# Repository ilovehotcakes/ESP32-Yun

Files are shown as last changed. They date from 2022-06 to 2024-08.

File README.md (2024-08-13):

# ESP32 Yun
An open-source, end-to-end hardward & software solution for motorizing your smart home.

ESP32 Yun is an affordable, reliable, and user-friendly wireless stepper motor controller that works with two-phase bipolar stepper motors. It comes with a web user-interface for intuitive controls and HTTP restful APIs for custom integrations.

Under active development.



<p align="center">
    
</p>

## Features
* 📡 WiFi-based: no need for extra hub
* 🔄 Closed-loop system: motor can be manually moved without losing track of its position
* 🛑 Automatic stalling detection and stopping: preventing injuries and protecting the motor
* 🤖 Custom hardware: few parts, cheap and relatively easy to assemble
* 🖥️ Web UI: no need to download app to control motor or change settings, works on desktop/mobile devices
* 🌐 HTTP restful APIs: easy to create integrations for smart home platforms
* 😶 Extremely quiet, won't even wake a baby!
* 🚀 Can go really fast!

Please see [demo video](images/demo_video.mp4) for full demonstration!

## Building your own
There are three components: electronics, firmware, and mounting hardware. ⚠️Requires basic knowledge of flashing firmware and soldering.

### Requirements:
* [USB-to-TTL serial adatper](https://www.amazon.com/dp/B07WX2DSVB) to upload the firmware
* Soldering iron, wires, and [JST PH connectors](https://www.amazon.com/dp/B0731MZCGF)/[crimper](https://www.amazon.com/dp/B00YGLKBSK)
* Two-phase bipolar stepper motor, such as a [Nema 11](https://www.amazon.com/dp/B00PNEPK94/)
* Magnet for the rotary encoder
* Power supply: 3.3-9V, 1.2A max
* (Optional) 3D printer for the motor mount

### 1. Electronics
Please refer to the [*electronics*](electronics/) folder.

**[[schematic](electronics/schematic.png)][[gerber files](electronics/gerber.zip)][[bom](electronics/bom.csv)][[pick-and-place file](electronics/pick_and_place.csv)]**
<p align="center">
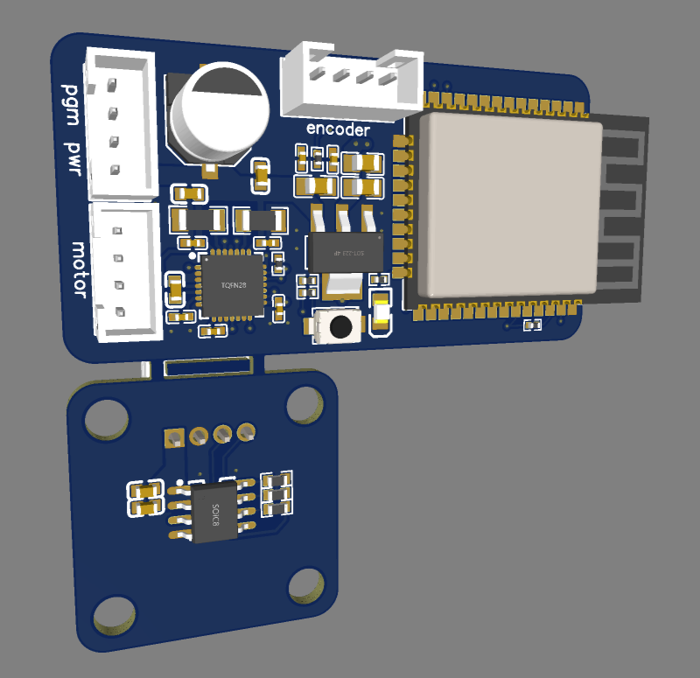
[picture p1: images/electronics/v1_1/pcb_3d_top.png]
    
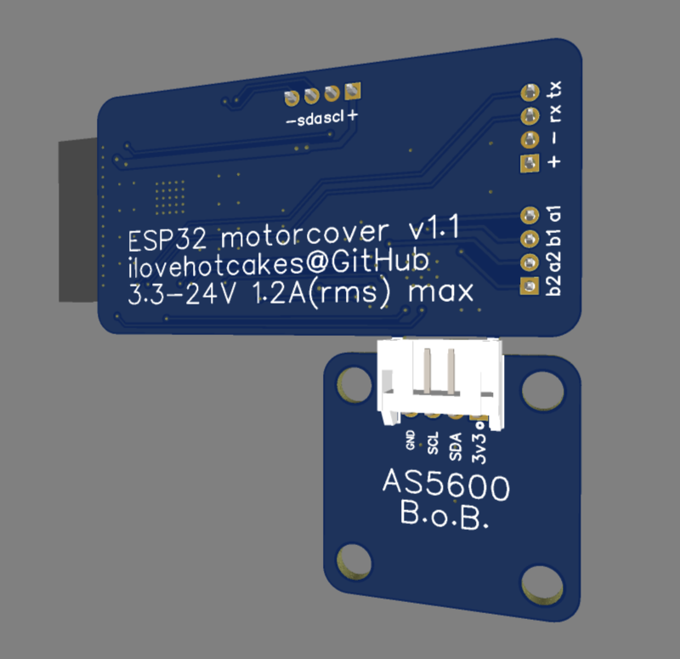
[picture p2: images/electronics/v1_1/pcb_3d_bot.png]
    
</p>

### 2. Firmware
Flash the firmware via [VSCode](https://code.visualstudio.com/) + [PlatformIO](https://platformio.org/install/ide?install=vscode).

#### Dependencies:
* espressif32@3.5.0
* [TMCStepper@^0.7.3](https://github.com/teemuatlut/TMCStepper)
* [FastAccelStepper@^0.27.5](https://github.com/gin66/FastAccelStepper/tree/0.27.5)
* [robtillaart/AS5600@^0.4.1](https://github.com/RobTillaart/AS5600/tree/0.4.1)
* [ESPAsyncWebServer](https://github.com/me-no-dev/ESPAsyncWebServer)
* [ArduinoJson@^7.0.4](https://github.com/bblanchon/ArduinoJson/tree/v7.0.4)
* [LittleFS_esp32@^1.0.6](https://github.com/lorol/LITTLEFS/tree/1.0.6)

#### Steps:
1. Clone this repository.
2. Double check and set proper current sense resistor value in **platformio.ini**.
3. Set the USB-to-TTL serial adatper's logic level to **3V3** and plug it in to the computer.
4. Keep holding the button on ESP32 Yun and start flashing the firmware.
5. Once the IDE begins data transmition, connect the four wires from ESP32 Yun to the adapter: **RX to TXD**, **TX to RXD**, **+ to VCC**, and **− to GND**.
6. Let go of the button once the firmware starts uploading. Unplug ESP32 motorcover after the firmware has finished uploading.

### 3. Mounting hardware
You can find the stl and pre-sliced files under the [*cad*](cad/) folder. To mount the magnet for the rotary encoder, it is recommended to use the manget gluing jig to make sure that the magnet is centered on the axis-of-rotation; otherwise, it could affect the accuracy of the rotary encoder.

#### Parts:
* Nema 11 motor mount: [[**stl**](cad/nema_11_motor_mount.stl)]
* AS5600 magnet gluing jig: [[**stl**](cad/prototype/magnet_gluing_jig_v1.stl)]
* AS5600 rotary encoder mount: [[**stl**](cad/as5600_mount.stl)]

<p align="center">
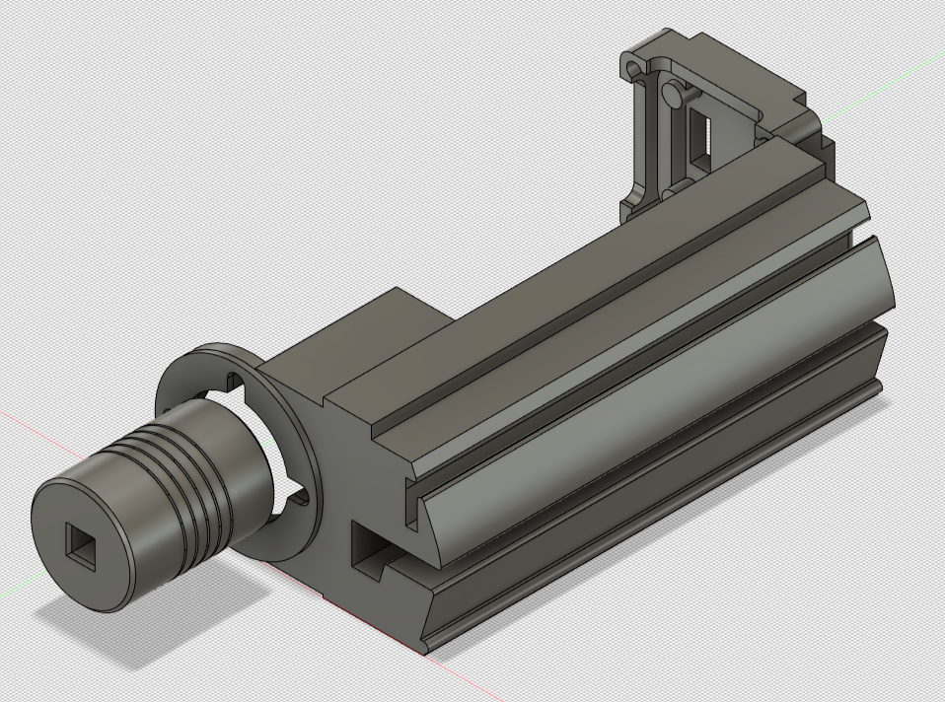
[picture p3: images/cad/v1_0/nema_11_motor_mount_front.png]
    
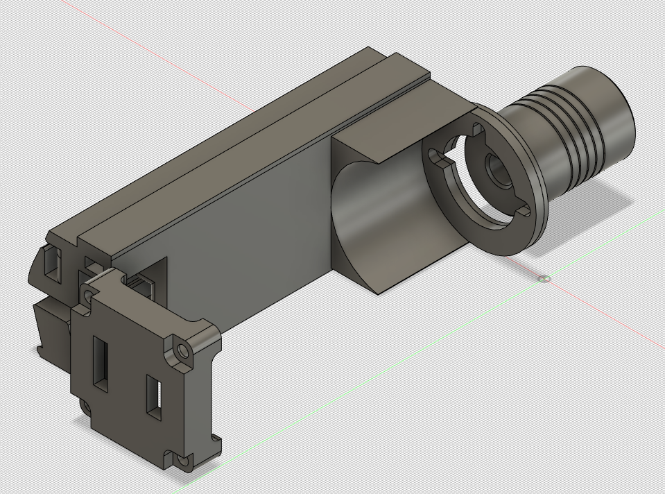
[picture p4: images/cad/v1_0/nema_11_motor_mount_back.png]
    
    </br>
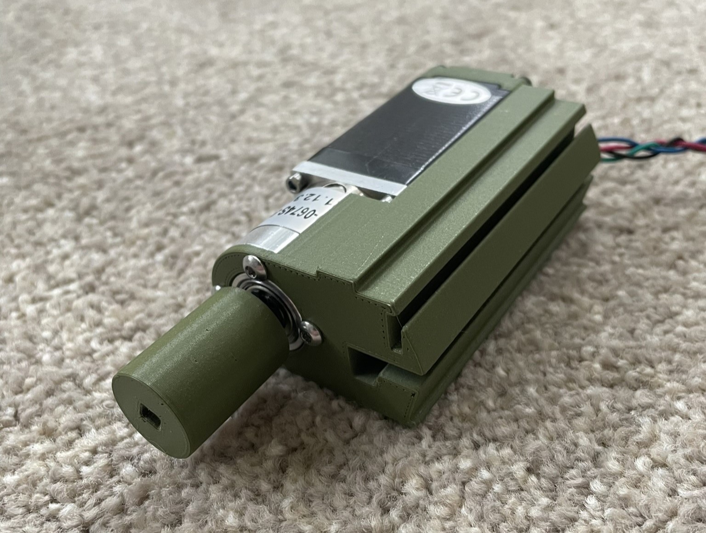
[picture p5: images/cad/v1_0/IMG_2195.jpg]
    
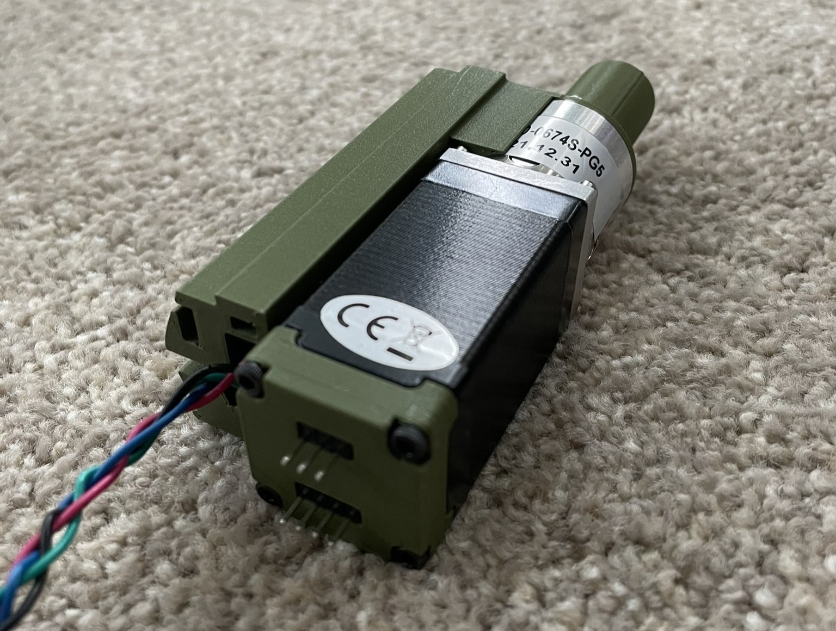
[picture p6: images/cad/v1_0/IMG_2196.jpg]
    
</p>

## Usage
During the first time booting up, ESP32 Yun is put into setup mode and it functions as a WiFi access point. Connect to it with your device like you would connect to a WiFi network. After connection is established, open a web browser and go to the IP address **[192.168.4.1]()** to access the web UI. There you can enter your WiFi network credentials and change other settings.

### HTTP Restful API
All RestAPIs are implemented as HTTP GET requests. To control the motor or change any settings, use [http://&lt;ESP32-YUN-IP-ADDRESS&gt;/&lt;URI&gt;?&lt;PARAM&gt;=&lt;VALUE&gt;](). For example: [http://192.168.4.1/motor?percent=0](). There are four URIs: motor, system, wireless, and json.

#### Motor params:
* stop: stop the motor
* percent: move the motor to the specified percentage
* step: move the motor to the specified step
* forward: run the motor foward continuously
* backward: run the motor backward continuously
* set-min: set the beginning endpoint
* set-max: set the ending endpoint
* zero: set the current motor position to zero
* standby: put the motor driver into standby to reduce power consumption
* sync-settings: sync open/closing settings for current, velocity, and acceleration 
* velocity: set both opening and closing velocity
* opening-velocity: set opening velocity
* closing-velocity: set closing velocity
* acceleration: set opening and closing acceleration
* opening-acceleration: set opening acceleration
* closing-acceleration: set closing acceleration
* current: set opening and closing current
* opening-current: set opening current
* closing-current: set closing current
* direction: change the direction of the motor
* full-steps: set the number of full steps per turn
* microsteps: set the number of subvisions per full step
* stallguard: enable/disable stallguard
* coolstep-threshold: set threshold to enable stallguard and coolstep
* stallguard-threshold: set threshold to trigger stallguard
* fastmode: set to exclusively use fastmode, i.e. SpreadCycle
* fastmode-threshold: set threshold to automatically switch over to fastmode

#### System params:
* sleep: put ESP32 Yun into standby
* restart: restart the system
* reset: reset all settings to factory settings
* name: rename the system

#### Wireless params:
* setup: setup mode
* ssid: ssid of your WiFi network
* password: passowrd of your WiFi network

#### Json:
Use HTTP GET request [http://&lt;ESP32-YUN-IP-ADDRESS&gt;/json]() to get all settings in a Json object.

### Button
* Toggle setup mode: press and hold down for 5 seconds till the led turns on
* Factory reset: press and hold down for 15 seconds till the led turns off after it turns on at 5 seconds

### (Optional) tuning StallGuard4
StallGuard4 (SG) is a feature of the motor driver, TMC2209, which provides automatic stall detection and stopping. SG requires some trial-and-error as well as some patience to get it working correctly. Please refer to the [TMC2209 datasheet](https://www.analog.com/media/en/technical-documentation/data-sheets/TMC2209_datasheet_rev1.09.pdf), chapter 16, page 70.

## In the works
* Custom drivers to reduce dependency and firmware size
* Updating PCB so little-to-no soldering is required
* Replace ESP32 WROOM 32E so USB-to-TTL is not required to flash the firmware
* BLE support
* Ultra-low power for battery application

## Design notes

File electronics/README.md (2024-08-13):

# Electronics
Here are two ways to acquire the electronics: **(1)** directly order printed circuit boards from online PCB services, or **(2)** buying breakout boards and assembling them on a breadboard.

## Option 1 - Ordering PCB from JLCPCB:
1. Download [gerber.zip](gerber.zip) and upload it to [JLCPCB.com](https://jlcpcb.com/). The only setting that needs to be changed is the **"Impedance Control"**. Select **"Yes"** and choose **"JLC0416H-3313"** once the dialog pops up.
2. If you prefer to have the PCB assembled by JLCPCB (additional cost), download the [pick-and-place.csv](pick_and_place.csv) and [bom.csv](bom.csv), and select **"PCB Assembly"**. Click on **"Confirm"** to go the next page.
3. Upload the pick-and-place and bom files. Click **"Process BOM & CPL"** and **"Continue"** when the error pops up. The error is for the missing connectors which will need to be manually solder once the PCBs arrive.
4. Place the order.
5. Once the PCBs arrive, solder connectors **J1-J4** and separate the AS5600 break-off board from the main board.
6. Crimp some 4-pin JST PH connectors and connect the stepper motor to the **"motor"** connector, power supply to the **"pwr"** connector, and AS5600 breakoff board to the **"encoder"** connector.
<p align="center">
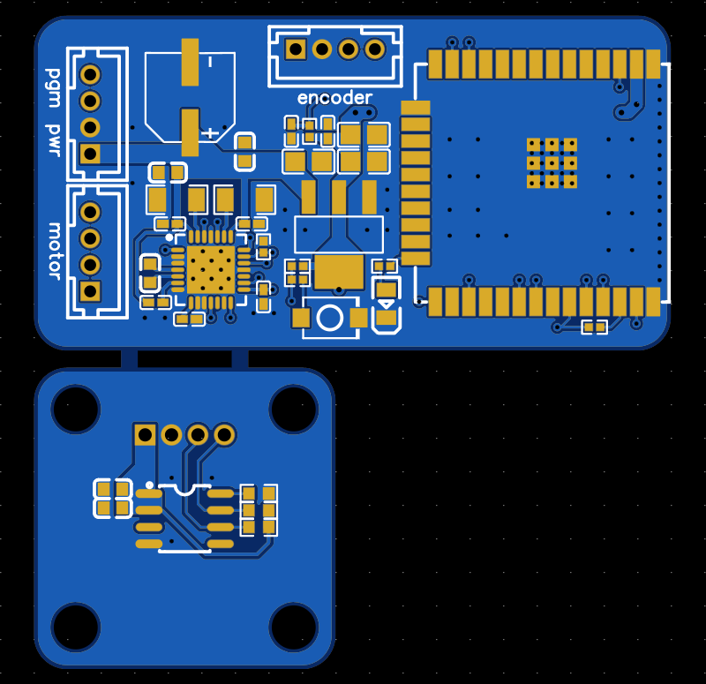
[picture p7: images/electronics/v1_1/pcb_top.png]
    
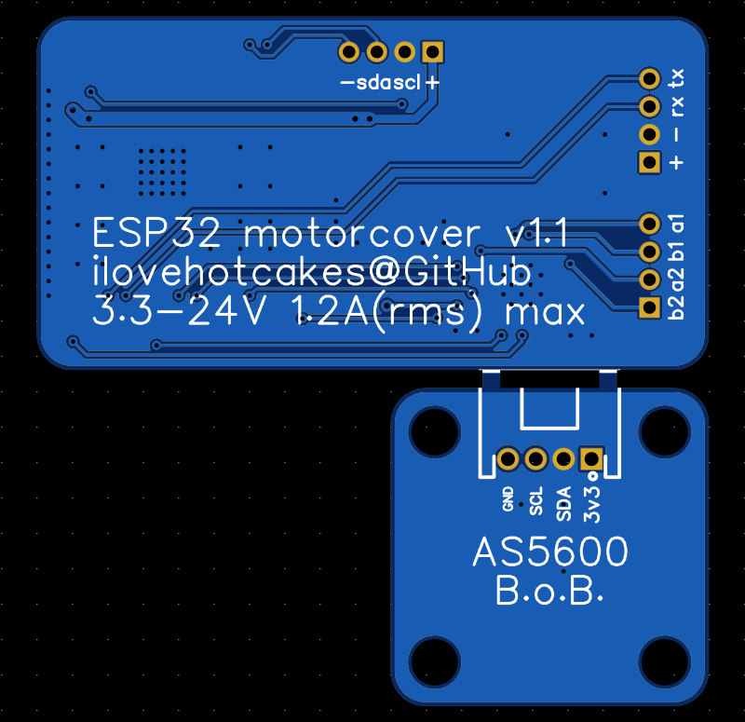
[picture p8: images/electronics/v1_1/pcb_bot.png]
    
</p>

## Option 2 - Breadboarding with breakout modules:
Both [TMC2209](https://www.amazon.com/dp/B07ZQ3C1XW) and [AS5600](https://www.amazon.com/dp/B09KGWC1PT/) come in breakout board packages which can be purchased from Amazon/AliExpress and assembled on a solderless breadboard. Please refer to this version of the [bom](prototype/bom.csv) and reference the schematic to assemble the circuit.
<p align="center">
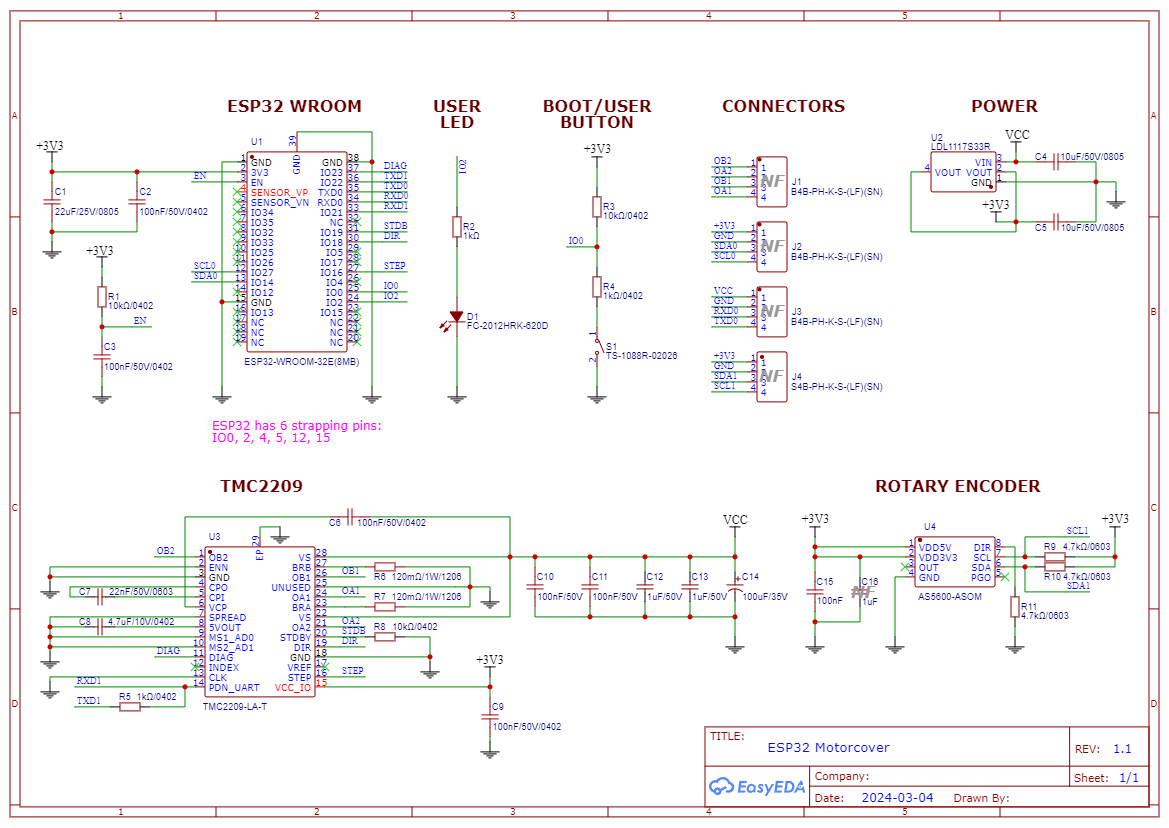
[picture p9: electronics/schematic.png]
    
</p>

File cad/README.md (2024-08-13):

# Mounting Hardware
If you don't own a 3D printer, consider online 3D printing services like [Shapeways](https://www.shapeways.com/) or local print farms.

## Recommendations
Print in TPU to reduce vibration and noise.

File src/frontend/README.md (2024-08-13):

The frontend is consisted of a single index.html webpage, however, it is split into three separate files in this directory: index.html, index.css, index.js for ease of development. The final index webpage needs to be assembled into one html file and stored as a string variable so it can be read by the wireless task.

The python script, index_script.py, reads and assembles the files from this directory and writes the output file index.h to the include directory. If you are using platformio, the frontend will be automatically generated when building the project; else, manually run the python script or copy-and-paste the files together.

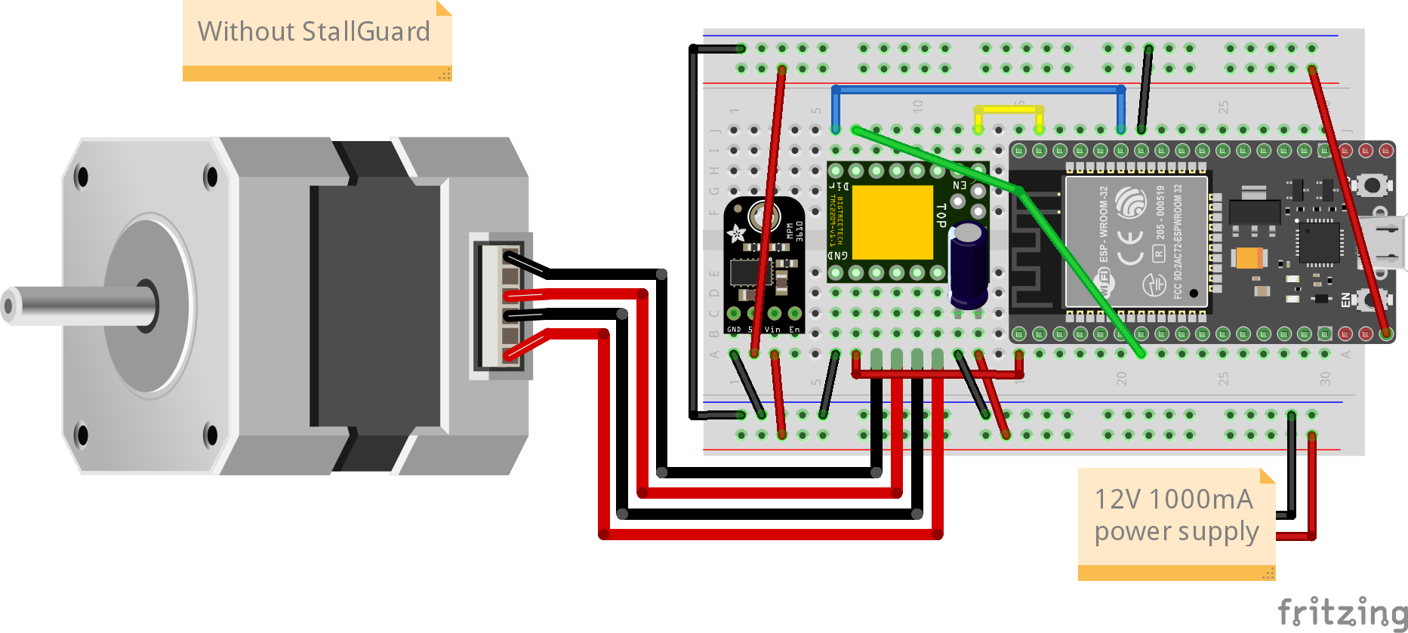
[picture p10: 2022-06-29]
electronics/prototype/esp32_motorcover.png

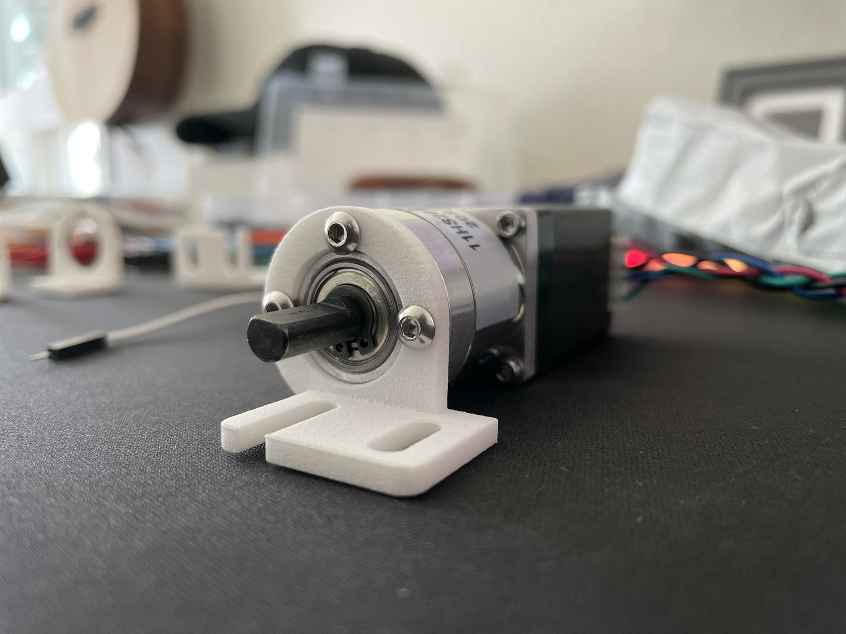
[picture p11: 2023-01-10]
images/cad/prototype/motor_in_mount.jpg

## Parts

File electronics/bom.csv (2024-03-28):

ID | Name | Designator | Footprint | Quantity | Manufacturer Part | Manufacturer | Supplier | Supplier Part | Price
1 | 100nF | C15 | C0603 | 1 | CC0603KRX7R9BB104 | YAGEO(国巨) | LCSC | C14663 | 0.002
2 | 100uF/35V | C14 | CAP-SMD_BD6.3-L6.6-W6.6-FD | 1 | EEEFT1V101AP | PANASONIC(松下) | LCSC | C128464 | 0.236
3 | ESP32-WROOM-32E(8MB) | U1 | WIFI-SMD_ESP32-WROOM-32E | 1 | ESP32-WROOM-32E-N8 | ESPRESSIF(乐鑫) | LCSC | C701342 | 3.284
4 | LDL1117S33R | U2 | SOT-223-4_L6.5-W3.5-P2.30-LS7.0-BR | 1 | LDL1117S33R | ST(意法半导体) | LCSC | C435835 | 0.177
5 | TMC2209-LA-T | U3 | QFN-28_L5.0-W5.0-P0.50-BL-EP | 1 | TMC2209-LA-T | TRINAMIC | LCSC | C2150710 | 2.449
6 | AS5600-ASOM | U4 | SOIC-8_L5.0-W4.0-P1.27-LS6.0-BL | 1 | AS5600-ASOM | ams(艾迈斯半导体) | LCSC | C79815 | 1.441
7 | 22uF/25V/0805 | C1 | C0805 | 1 | CL21A226MAQNNNE | SAMSUNG(三星) | LCSC | C45783 | 0.025
8 | 100nF/50V/0402 | C2,C3,C6,C9 | C0402 | 4 | CL05B104KB54PNC | SAMSUNG(三星) | LCSC | C307331 | 0.005
9 | 10uF/50V/0805 | C4,C5 | C0805 | 2 | GRM21BR61H106KE43L | muRata(村田) | LCSC | C440198 | 0.07
10 | 22nF/50V/0603 | C7 | C0603 | 1 | CL10B223KB8NNNC | SAMSUNG(三星) | LCSC | C21122 | 0.004
11 | 4.7uF/10V/0402 | C8 | C0402 | 1 | CL05A475MP5NRNC | SAMSUNG(三星) | LCSC | C23733 | 0.006
12 | 100nF/50V | C10,C11 | C0402 | 2 | CL05B104KB54PNC | SAMSUNG(三星) | LCSC | C307331 | 0.005
13 | 1uF/50V | C12,C13 | C0603 | 2 | CL10A105KB8NNNC | SAMSUNG(三星) | LCSC | C15849 | 0.005
14 | 10kΩ/0402 | R1,R3,R8 | R0402 | 3 | 0402WGF1002TCE | UNI-ROYAL(厚声) | LCSC | C25744 | 0.001
15 | 1kΩ | R2 | R0402 | 1 | 0402WGF1001TCE | UNI-ROYAL(厚声) | LCSC | C11702 | 0.001
16 | 1kΩ/0402 | R4,R5 | R0402 | 2 | 0402WGF1001TCE | UNI-ROYAL(厚声) | LCSC | C11702 | 0.001
17 | 120mΩ/1W/1206 | R6,R7 | R1206 | 2 | STE1206M1W0R120F | WALTER(华德) | LCSC | C201309 | 0.054
18 | 4.7kΩ/0603 | R9,R10,R11 | R0603 | 3 | 0603WAF4701T5E | UNI-ROYAL(厚声) | LCSC | C23162 | 0.001
19 | TS-1088R-02026 | S1 | SW-SMD_L3.9-W3.0-P4.45 | 1 | TS-1088R-02026 | XUNPU(讯普) | LCSC | C455280 | 0.049
20 | FC-2012HRK-620D | D1 | LED0805-R-RD | 1 | NCD0805R1 | 国星光电 | LCSC | C84256 | 0.012

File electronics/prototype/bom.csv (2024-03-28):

Item | Cost (incl. tax) | Quantity | Shipping | Subtotal | Vendor | Links
NEMA bipolar stepper motor | 33.34 | 5 | 33.12 | 199.82 | Stepperonline | https://www.omc-stepperonline.com/nema-11-stepper-motor-bipolar-l-45mm-w-gear-ratio-5-1-planetary-gearbox-11hs18-0674s-pg5
ESP32 node mcu | 12.1 | 5 |  | 60.5 | Amazon | https://www.amazon.com/dp/B0718T232Z
Buck convertor | 5.95 | 5 | 7.99 | 37.74 | Mouser | https://www.mouser.com/ProductDetail/485-4739
TMC2209 UART stepper driver | 34.12 | 1 |  | 34.12 | Amazon | https://www.amazon.com/gp/product/B07YW7BM68
Coupling | 14.96 | 1 |  | 14.96 | Amazon | https://www.amazon.com/gp/product/B07MPFJGZW
100uF capacitor | 6.82 | 1 |  | 6.82 | Amazon | https://www.amazon.com/gp/product/B07Y3F194W
Solderless breadboard | 6.59 | 1 |  | 6.59 | Amazon | https://www.amazon.com/gp/product/B07LF71ZTS
Power supply | 17.51 | 2 |  | 35.02 | Amazon | https://www.amazon.com/gp/product/B07N18XN84
Wires | 14.86 | 1 |  | 14.86 | Amazon | https://www.amazon.com/gp/product/B07Z4W6V6R
Mounting bracket (Shapeways) | 6.04 | 5 | 9.99 | 40.2 | Shapeways | resources/mounting_bracket_v3.stl
Screws | 10 | 1 |  | 10
AS5600 | 16.99 |  |  | 16.99 | Amazon | https://www.amazon.com/dp/B097QNG1CN
Total |  |  |  | 477.62

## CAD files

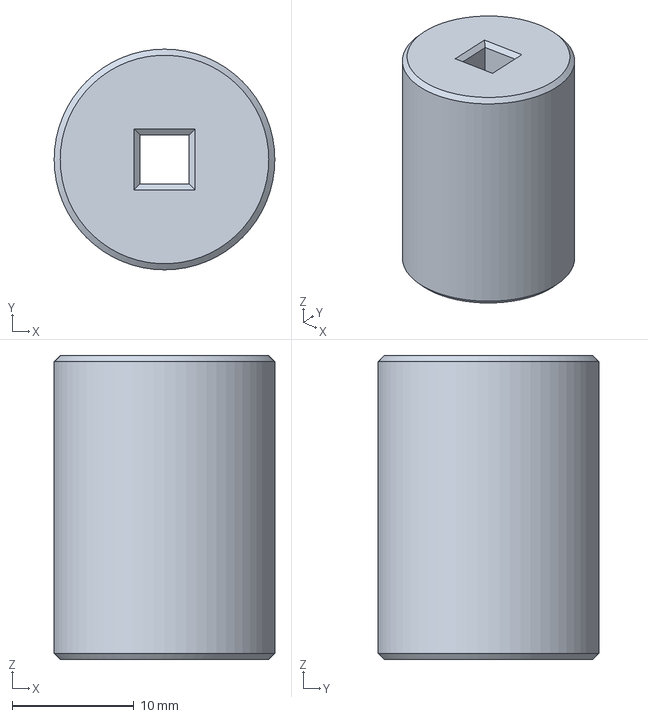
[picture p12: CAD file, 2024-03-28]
cad/coupling.3mf
18.1 x 18.1 x 25.0 mm

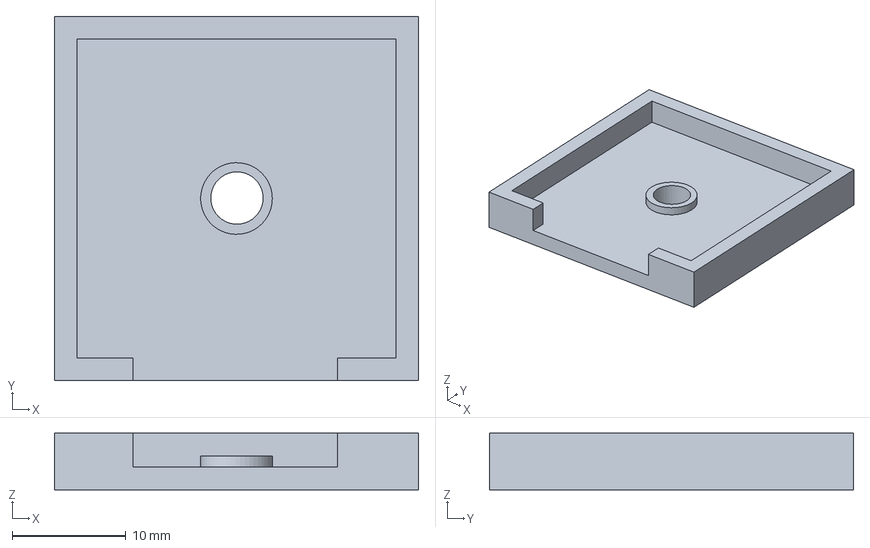
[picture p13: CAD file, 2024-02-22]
cad/prototype/magnet_gluing_jig_v1.3mf
32.0 x 32.0 x 5.00 mm

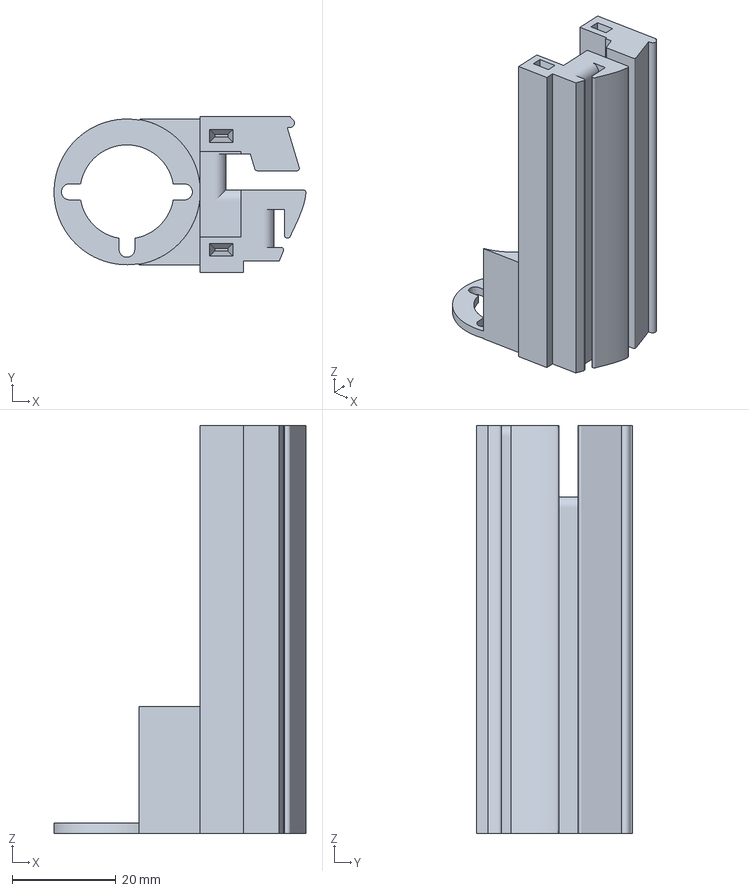
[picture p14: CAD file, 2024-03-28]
cad/nema_11_motor_mount.3mf
48.7 x 30.2 x 78.8 mm

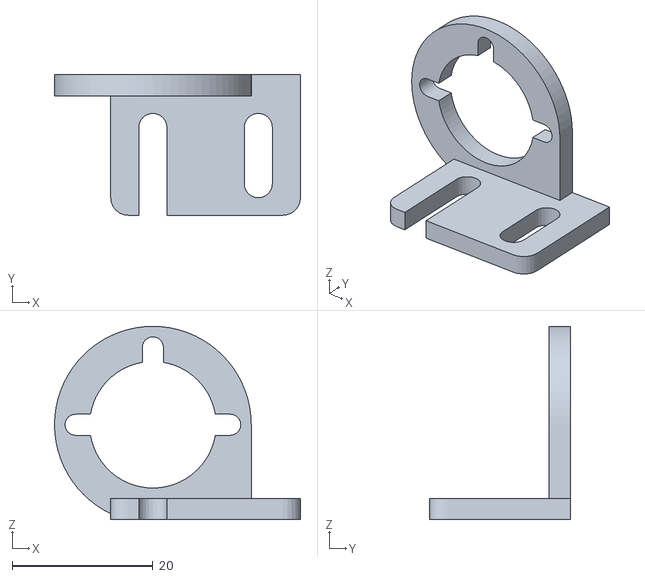
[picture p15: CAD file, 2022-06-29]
cad/prototype/nema11_mount_v3.stl
35.0 x 20.0 x 27.5

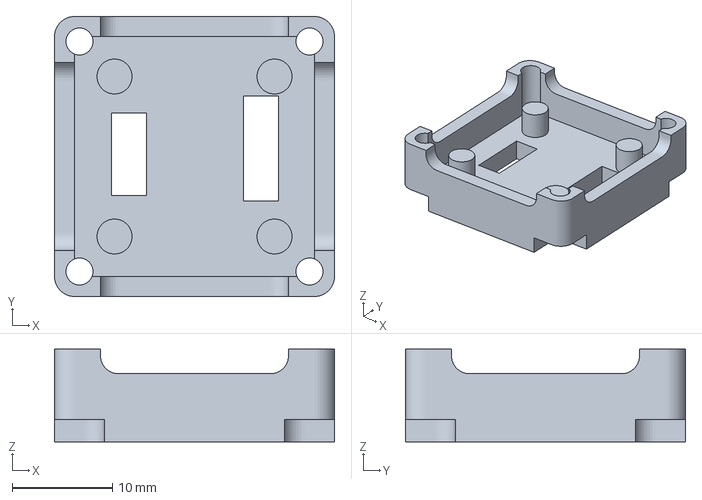
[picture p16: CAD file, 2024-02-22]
cad/as5600_mount.3mf
28.0 x 28.0 x 9.25 mm

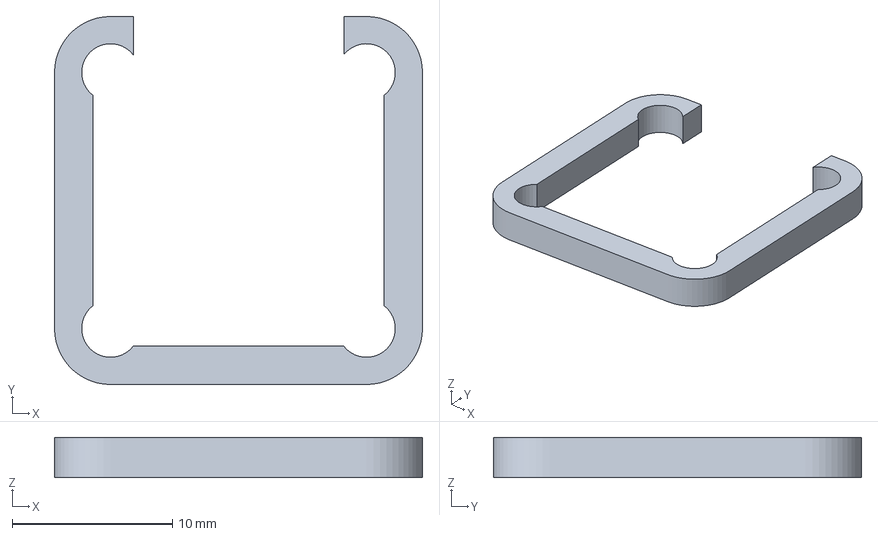
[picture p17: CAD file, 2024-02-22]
cad/as5600_mount_insert.3mf
23.0 x 23.0 x 2.50 mm

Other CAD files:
cad/prototype/nema11_mount_v3_mirrored.stl
cad/as5600_mount.stl
cad/as5600_mount_insert.stl
cad/coupling.stl
cad/magnet_gluing_jig_v1.stl
cad/nema_11_motor_mount.stl
cad/prototype/magnet_gluing_jig_v1.stl

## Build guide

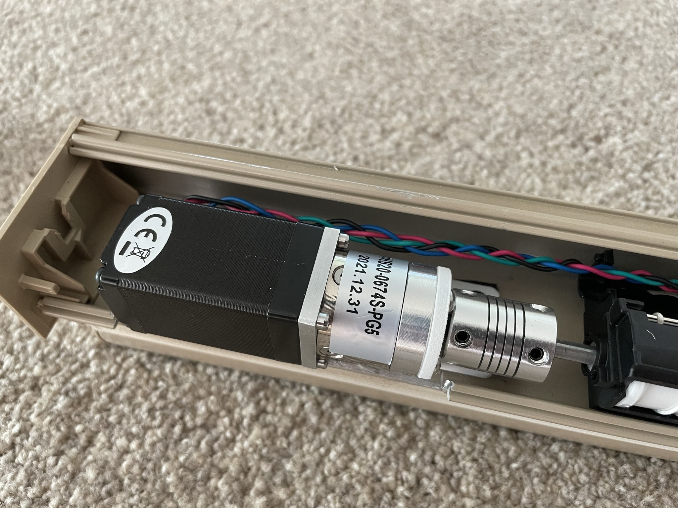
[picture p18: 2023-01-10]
images/cad/prototype/motor_installed.jpg

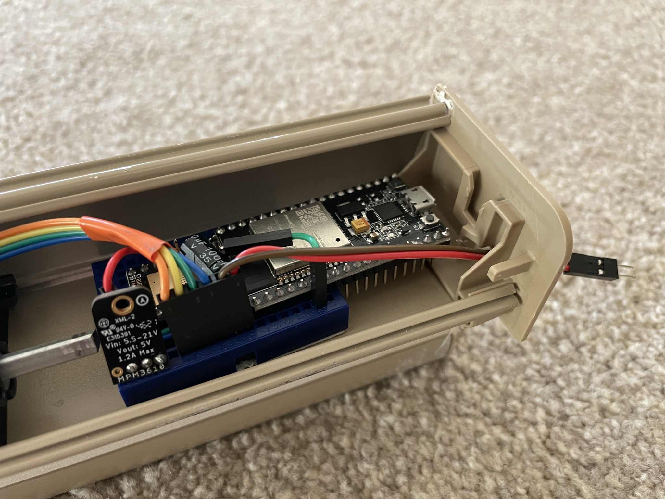
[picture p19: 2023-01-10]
images/electronics/prototype/controller_installed.jpg

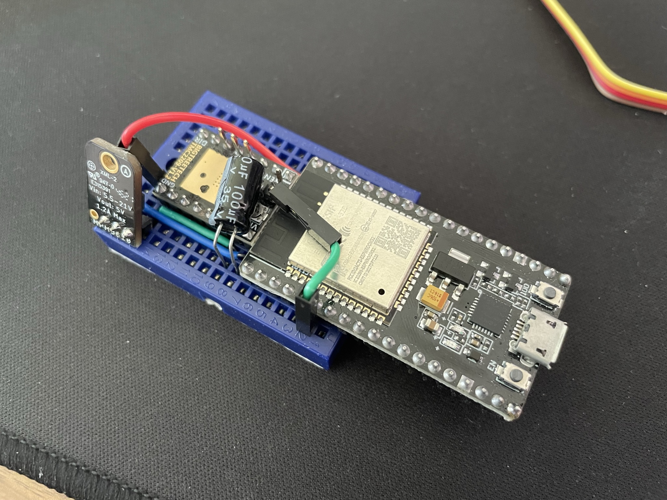
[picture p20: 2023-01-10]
images/electronics/prototype/assembled_controller.jpg

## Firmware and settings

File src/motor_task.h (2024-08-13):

#pragma once
/**
    motor_task.h - A class that contains all functions to control a two-phase bipolar stepper motor.
    Author: Jason Chen, 2022

    The MCU sends PWM signals to the stepper motor driver, TMC2209, to control the current to the
    motor and thereby moving the motor. Higher voltages and current generate more torque and higher
    RPMs. To operate the driver: (1) start the driver by taking it out of STANDBY, and (2) ENABLE
    the motor coils. Both are done automatically.

    The position of the system is absolute and it is translated between 3 different methods:
        (1) "Position" refers to the encoder's position, used for internal position tracking
        (2) "Steps" refers to the motor's position, used for moving the motor
        (3) "Percentage" refers to the overall percentage, used by UI
**/
#include <HardwareSerial.h>       // Hardwareserial for uart
#include <FunctionalInterrupt.h>  // std:bind()
#include <TMCStepper.h>
#include <FastAccelStepper.h>
#include <AS5600.h>
#include "task.h"


#define DEFAULT_MOTOR_FULLSTEPS   200      // NEMA motors have 200 full steps/rev
#define DEFAULT_ENCODER_POSITIONS 4096.0f  // AS5600 absolute position is 12-bit


class MotorTask : public Task {
public:
    MotorTask(const uint8_t task_core);
    ~MotorTask();
    void addWirelessTask(Task *task);
    void addSystemSleepTimer(xTimerHandle timer);

protected:
    void run();

private:
    // TMCStepper library for interfacing with the stepper motor driver hardware, to read/write
    // registers for setting speed, acceleration, current, etc.
    TMC2209Stepper driver_ = TMC2209Stepper(&Serial1, R_SENSE, DRIVER_ADDR);

    // User adjustable TMC2209 motor driver settings, updated to driver registers via UART
    bool  driver_stdby_  = false;
    bool  sync_settings_ = false;  // If false, opeining/closing settings are different values
    float open_velocity_ = 3.0;
    float clos_velocity_ = 3.0;
    float open_accel_    = 0.5;
    float clos_accel_    = 0.5;
    int   open_current_  = 200;
    int   clos_current_  = 75;
    bool  direction_     = false;
    int   microsteps_    = 2;
    int   full_steps_    = DEFAULT_MOTOR_FULLSTEPS;
    bool  stallguard_en_ = true;
    int   coolstep_thrs_ = 0;
    int   stallguard_th_ = 10;
    bool  spreadcycl_en_ = false;
    int   spreadcycl_th_ = 33;

    // FastAccelStepper library for generating PWM signal to the stepper driver to move/accelerate
    // and stop/deccelerate the stepper motor.
    FastAccelStepperEngine engine_ = FastAccelStepperEngine();
    FastAccelStepper *motor_       = NULL;

    // None user adjustable motor states. Managed by MotorTask.
    int8_t  last_updated_percent_ = -100;
    volatile bool stalled_        = false;
    portMUX_TYPE stalled_mux_     = portMUX_INITIALIZER_UNLOCKED;
    // bool motor_opening = false;
    // bool motor_closing = false;
    // bool motor_move_completed = false;

    // Rotary encoder for keeping track of motor's actual position because motor could slip and
    // cause the position to be incorrect. A closed-loop system.
    AS5600 encoder_;

    // Keeping track of the overall position via encoder's position and then  convert it into
    // motor's position and percentage.
    int32_t encod_offset_      = 0;
    int32_t encod_pos_         = 0;
    int32_t encod_max_pos_     = static_cast<int32_t>(DEFAULT_ENCODER_POSITIONS) * 10;
    int   total_steps_         = full_steps_ * microsteps_;
    float motor_encoder_ratio_ = total_steps_ / DEFAULT_ENCODER_POSITIONS;
    float encoder_motor_ratio_ = DEFAULT_ENCODER_POSITIONS / total_steps_;

    Task *wireless_task_;              // To receive messages from wireless task
    xTimerHandle system_sleep_timer_;  // To prevent system from sleeping before motor stops

    void stallguardInterrupt();
    void loadSettings();  // Load motor settings from flash
    bool prepareToMove(bool check, bool direction);
    void move(bool direction);
    void moveToStep(int target_step);
    void moveToPercent(int target_percent);
    void stop();
    bool setMin();
    bool setMax();
    bool zeroEncoder();
    bool motorEnable(uint8_t enable_pin, uint8_t value);
    void calculateTotalSteps();
    inline int getPercent();
    inline int positionToStep(int encoder_position);
    // For quick configuration guide, please refer to p70-72 of TMC2209's datasheet rev1.09
    // TMC2209's UART interface automatically becomes enabled when correct UART data is sent. It
    // automatically adapts to uC's baud rate. Block until UART is finished initializing so ESP32
    // can send settings to the driver via UART.
    void updateMotorSettings(float velocity, float acceleration, int current);
    void driverStartup();
    void driverStandby();
};

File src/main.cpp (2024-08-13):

/**
    Aurthor: Jason Chen, 2022
    Licence: TODO

    An ESP32-based low-powered wireless motor controller that works with two-phase bipolar stepper
    motors. It is a closed-loop system so it is capable of keeping track of its position even when
    the motor is off.

    You can use it to motorize and automate the opening & closing of blinds/shades/windows etc.
**/
#include "system_task.h"
#include "motor_task.h"
#include "wireless_task.h"


static WirelessTask wireless_task(0);  // Running on core0
static SystemTask system_task(0);      // Running on core0
static MotorTask motor_task(1);        // Running on core1


void setup() {
    // Initializing serial output if compiled
    LOG_INIT(115200, LogLevel::INFO);

    if (!LITTLEFS.begin(true)) {
        LOGE("Failed to mount filesystem");
    }

    // setCpuFrequencyMhz(80);

    system_task.init();
    system_task.addMotorTask(&motor_task);
    system_task.addWirelessTask(&wireless_task);

    wireless_task.init();
    wireless_task.addMotorTask(&motor_task);
    wireless_task.addSystemTask(&system_task);
    wireless_task.addSystemSleepTimer(system_task.getSystemSleepTimer());

    motor_task.init();
    motor_task.addWirelessTask(&wireless_task);
    motor_task.addSystemSleepTimer(system_task.getSystemSleepTimer());

    // Delete setup/loop task
    vTaskDelete(NULL);
}


void loop() {}

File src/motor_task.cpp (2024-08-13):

#include "motor_task.h"


MotorTask::MotorTask(const uint8_t task_core) : Task{"MotorTask", 8192, 1, task_core} {}
MotorTask::~MotorTask() {}


void MotorTask::run() {
    pinMode(DIR_PIN, OUTPUT);
    pinMode(STEP_PIN, OUTPUT);
    pinMode(STBY_PIN, OUTPUT);
    pinMode(DIAG_PIN, INPUT);

    // Using UART(Serial1) to read/write data to/from TMC2209 stepper motor driver
    Serial1.begin(115200, SERIAL_8N1, RXD1, TXD1);
    while(!Serial1);

    // FastAccelStepper setup
    engine_.init(1);
    motor_ = engine_.stepperConnectToPin(STEP_PIN);
    assert(motor_ != NULL);
    motor_->setEnablePin(100, false);
    motor_->setExternalEnableCall(std::bind(&MotorTask::motorEnable, this,
                                  std::placeholders::_1, std::placeholders::_2));
    motor_->setDirectionPin(DIR_PIN);
    motor_->setAutoEnable(true);     // Automatically enable/disable motor output when moving
    motor_->setDelayToDisable(200);  // 200ms off delay

    driverStandby();

    // AS5600 rotary encoder setup
    encoder_.begin(SDA_PIN, SCL_PIN);
    // assert(encoder_.isConnected());
    Wire.setClock(1000000);         // Increase I2C bus speed to 1MHz which is AS5600's max bus speed
    encoder_.setConfigure(0x2904);  // Hysteresis=1LSB, fast filter=10LSBs, slow filter=8x, WD=ON
    LOGI("Encoder automatic gain control(56-68 is preferable): %d/128", encoder_.readAGC());

    loadSettings();
    // int start = 0;
    while (1) {
        // start = micros();
        encod_pos_ = encoder_.getCumulativePosition() - encod_offset_;
        motor_->setCurrentPosition(positionToStep(encod_pos_));

        if (xQueueReceive(queue_, (void*) &inbox_, 0) == pdTRUE) {
            LOGI("MotorTask received message: %s", inbox_.toString().c_str());
            switch (inbox_.command) {
                case MOTOR_STOP:
                    stop();
                    break;
                case MOTOR_PERECENT:
                    moveToPercent(inbox_.parameter);
                    break;
                case MOTOR_STEP:
                    moveToStep(inbox_.parameter);
                    break;
                case MOTOR_FORWARD:
                    move(false);
                    break;
                case MOTOR_BACKWARD:
                    move(true);
                    break;
                case MOTOR_SET_MIN:
                    setMin();
                    break;
                case MOTOR_SET_MAX:
                    setMax();
                    break;
                case MOTOR_ZERO:
                    zeroEncoder();
                    break;
                case MOTOR_STANDBY:
                    if (inbox_.parameter == 1) driverStandby();
                    else driverStartup();
                    break;
                case MOTOR_SYNC_STTNG:
                    setAndSave(sync_settings_, static_cast<bool>(inbox_.parameter), "sync_settings_");
                    break;
                case MOTOR_VLCTY:
                    setAndSave(open_velocity_, inbox_.parameterf, "open_velocity_");
                    setAndSave(clos_velocity_, inbox_.parameterf, "clos_velocity_");
                    break;
                case MOTOR_OP_VLCTY:
                    setAndSave(open_velocity_, inbox_.parameterf, "open_velocity_");
                    break;
                case MOTOR_CL_VLCTY:
                    setAndSave(clos_velocity_, inbox_.parameterf, "clos_velocity_");
                    break;
                case MOTOR_ACCEL:
                    setAndSave(open_accel_, inbox_.parameterf, "open_accel_");
                    setAndSave(clos_accel_, inbox_.parameterf, "clos_accel_");
                    break;
                case MOTOR_OP_ACCEL:
                    setAndSave(open_accel_, inbox_.parameterf, "open_accel_");
                    break;
                case MOTOR_CL_ACCEL:
                    setAndSave(clos_accel_, inbox_.parameterf, "clos_accel_");
                    break;
                case MOTOR_CURRENT:
                    setAndSave(open_current_, inbox_.parameter, "open_current_");
                    setAndSave(clos_current_, inbox_.parameter, "clos_current_");
                    break;
                case MOTOR_OP_CURRENT:
                    setAndSave(open_current_, inbox_.parameter, "open_current_");
                    break;
                case MOTOR_CL_CURRENT:
                    setAndSave(clos_current_, inbox_.parameter, "clos_current_");
                    break;
                case MOTOR_DIRECTION:
                    setAndSave(direction_, static_cast<bool>(inbox_.parameter), "direction_");
                    break;
                case MOTOR_FULL_STEPS:
                    setAndSave(full_steps_, inbox_.parameter, "full_steps_");
                    calculateTotalSteps();
                    break;
                case MOTOR_MICROSTEPS:
                    setAndSave(microsteps_, inbox_.parameter, "microsteps_");
                    calculateTotalSteps();
                    break;
                case MOTOR_STALLGUARD:
                    setAndSave(stallguard_en_, static_cast<bool>(inbox_.parameter), "stallguard_en_");
                    break;
                case MOTOR_TCOOLTHRS:
                    setAndSave(coolstep_thrs_, inbox_.parameter, "coolstep_thrs_");
                    break;
                case MOTOR_SGTHRS:
                    setAndSave(stallguard_th_, inbox_.parameter, "stallguard_th_");
                    break;
                case MOTOR_SPREADCYCL:
                    setAndSave(spreadcycl_en_, static_cast<bool>(inbox_.parameter), "spreadcycl_en_");
                    break;
                case MOTOR_TPWMTHRS:
                    setAndSave(spreadcycl_th_, inbox_.parameter, "spreadcycl_th_");
                    break;
            }
        }

        if (stalled_) {
            stop();
            stalled_ = false;
            LOGE("Motor stalled");
        }

        if (motor_->isRunning()) {
            xTimerStart(system_sleep_timer_, 0);
            continue;
        }

        if (last_updated_percent_ == getPercent()) {
            // Serial.println(micros() - start);
            continue;
        }

        // Send new position % if it has changed
        int current_percent = getPercent();
        if (current_percent >= 0 && current_percent <= 100) {
            last_updated_percent_ = current_percent;
            sendTo(wireless_task_, Message(UPDATE_POSITION, current_percent), 0);
        }
    }
}


void IRAM_ATTR MotorTask::stallguardInterrupt() {
    portENTER_CRITICAL(&stalled_mux_);
    stalled_ = true;
    portEXIT_CRITICAL(&stalled_mux_);
}
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

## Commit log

2022-03-13 Updated required libaries for stepper motor
2022-03-21 Added memory for last position and max position after power outage
2022-06-04 Switched to non-blocking mqtt API
2022-06-04 Motor controls working
2022-06-04 Completed motor class and connection class
2022-06-05 Motor and communication working
2022-06-05 Added flag for motor obj to indicate avail msg
2022-06-10 Added callback for motor to send messages
2022-06-10 Fixed function prototype name
    [main.cpp]
2022-06-11 Stallguard working but not when stopping
    [main.cpp]
2022-06-14 Switching MQTT pubsub lib and stepper lib
2022-06-14 Adopted fastaccelstepper and stallguard
    [main.cpp]
2022-06-25 Added motor state
2022-06-27 Added enum for motor state, split opn/cls RMS curr
2022-06-29 updated image; added 3d printing file
2022-06-29 Updated readme and adde resources
    [esp32_motorcover.fzz]
2022-06-29 Updated documentation
    [esp32_motorcover.fzz]
2022-06-29 Updated connections and fixed setmin SG bug
    [esp32_motorcover.fzz]
2023-10-31 Fixed wifi disconnection issue
    [main.cpp]
2023-12-01 changed to motor_task.h
2023-12-01 Working wireless task
2023-12-01 Removed WiFi.mode(WIFI_STA) to increase stability
    [wireless_task.cpp]
2023-12-03 Added GPIO pin def and AS5600 library
2023-12-03 MVP encoder reading and sending position updates
2023-12-05 Changed I2C data pin to GPIO5
2023-12-05 Removed gearboxratio since no longer needed
2023-12-05 Updated schematic
    [esp32_motorcover.fzz]
2023-12-05 Rotary encoder working for shades
2024-02-03 Fixed bug in moveToPercent
    [motor_task.cpp]
2024-02-18 Corrected tmc2099 to tmc2209
    [motor_task.cpp, motor_task.h]
2024-02-18 Added HardwareSerial.h for uart
2024-02-22 Uart motor enable; SG interrupt IRAM
2024-02-22 Specify espressif32@3.5.0 version; updated uart pins
2024-02-22 Updated GPIO pins to pcb layout
2024-02-22 File reorganization
    [nema11_mount_v3.stl, nema11_mount_v3_mirrored.stl]
2024-02-22 Moved tmc2209 variables to motor_task.h
2024-02-24 Fixed minor position calculation bug
    [motor_task.cpp]
2024-02-24 SG interrupt changed to 1 tick to not crash cpu
    [motor_task.cpp]
2024-03-05 Set button gpio; added delay to tasks startup
2024-03-05 Changed driver settings
2024-03-05 Changed shunt resistor to pcb value
2024-03-13 Reduced wireless queue size and wait time
2024-03-28 added as5600
    [bom.csv]
2024-04-09 Updated pins to pcb v1.1
2024-04-09 Added standby controls and moved driver init to func
2024-04-10 Changed motor to system message queue
2024-04-10 Successfully moving motor and sending comm to sys
2024-04-10 Automatic driver standby and startup
2024-04-12 Auto motor startup and reading from encoder OUT pin
2024-04-15 Added motor standby automation in wireless task
2024-04-15 Added system standby timer
2024-04-15 Automatic motor standby; motor command update
2024-04-15 Automatic motor driver standby
2024-04-16 ESP32 fast boot and gpio pin renaming
2024-04-16 Don't request to start driver if it's already started
2024-04-18 Updated method of setting fast/slow filters which is now effective
2024-04-18 Websocket server in AP mode working for LED on/off
2024-04-22 Removed motor_standby_sem_
2024-04-22 Encoder add WD and hysteresis setting
2024-04-23 Changed the delay time to 10ms to wait for driver to start up
2024-04-23 Added watchdog to wireless task and moved OTA
2024-04-27 Moved driver startup to move()
2024-04-29 Added commands for updating motor settings
2024-04-29 Updated button to make http requests
2024-04-29 Change some motor/driver setting to float
2024-04-29 Moved WDT init to wireless task
2024-04-29 Added motor setting preferences
2024-04-30 Added put/get preferences for all motor task variables
2024-04-30 Added prefetch check and no found error handling
    [wireless_task.cpp]
2024-05-02 Removed delay for motor task to not voluntarily yield
2024-05-10 moved led pinmode to system task
2024-05-14 added step, forward, backward motor apis
2024-05-14 Added buttons for forward, backward, set min, set max, automatic hide
2024-05-14 updated command and motor variable names, added variables for settings
2024-05-15 added loadSettings for all tasks, added button func for system task
2024-05-15 Added wireless commands and renamed reboot to restart
    [command.cpp, command.h]
2024-05-15 initialize fs in main to mount fs sooner
2024-05-15 added wireless commands to set ap_ssid_, sta_ssid_, sta_password_
2024-05-15 added button press to check for reset
    [motor_task.cpp, system_task.cpp, system_task.h]
2024-05-15 added macros, added led indicator for button presses
2024-05-15 added macros; added connection failed attempts
    [wireless_task.cpp]
2024-05-23 added navbar radio selection and wireless card
2024-05-24 Added motor settings html elements and css
2024-05-24 fixed saving serial_ and ap_ssid_ in initial setup
    [system_task.cpp, wireless_task.cpp]
2024-05-25 added motor zero api and changed default microsteps to 2
2024-05-25 fixed bug in move moveToPercent moveToStep where it doesn't stop when motor is running
    [motor_task.cpp, motor_task.h]
2024-05-28 refactored javascript functions for motor actions
2024-05-28 fixed bug in http request for ssid and password
    [wireless_task.cpp]
2024-05-29 replaced faux settings with real backend values
    [wireless_task.cpp]
2024-05-31 added show/hide buttons for motor control page and motor settings page
2024-06-01 increased StepperTask stack size to avoid stackoverflow
2024-06-01 moved delay of starting driver and updating driver setting to perspective functions
2024-06-03 wireless task sending string via int values to system task
2024-06-04 prevent handling http requests with with empty param names and values
    [wireless_task.cpp]
2024-06-04 added dropdown menu for motor and system settings
2024-06-05 added images for more settings button and back arrow
2024-06-06 moved attachinterrupt for sg to updateMotorSettings(); added check for driverStartup(); added delay after pulling STBY_PIN low
2024-06-09 updated the button checking if else flow
2024-06-10 fixed bug in resetting encod_pos_
    [motor_task.cpp, motor_task.h]
2024-06-10 updated css for mobile device
2024-06-10 added no-focus for checkbox on ios devices
